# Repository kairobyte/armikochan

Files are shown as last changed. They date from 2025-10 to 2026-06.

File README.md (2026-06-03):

# ARMIKOCHAN V2: 8 AXIS ROBOTIC ARM




This project is my 200+ day journey of building a high-precision, 8-degree-of-freedom robotic arm from scratch.

## The Vision

Most robotic arms out there are 6DOF at best, and they easily cost upwards of $5000. For a student or a smaller college, that's just not realistic. The ones that do offer more capability are either proprietary, locked behind expensive licenses, or simply too complex to learn from. There's a huge gap between what's available and what's actually accessible, and that gap is what this project is trying to fill.

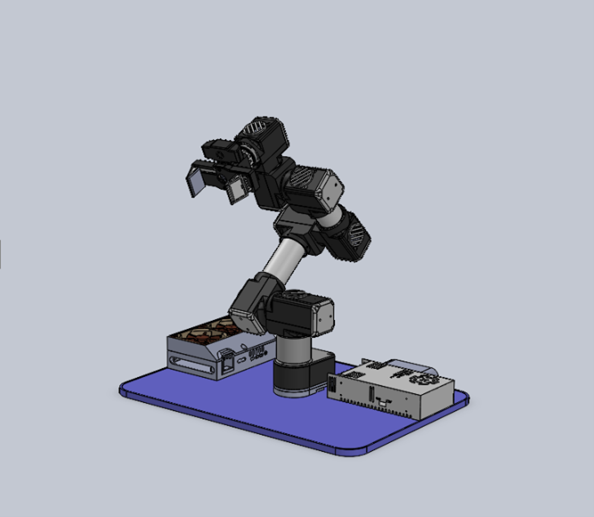
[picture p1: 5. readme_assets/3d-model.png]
3d-model
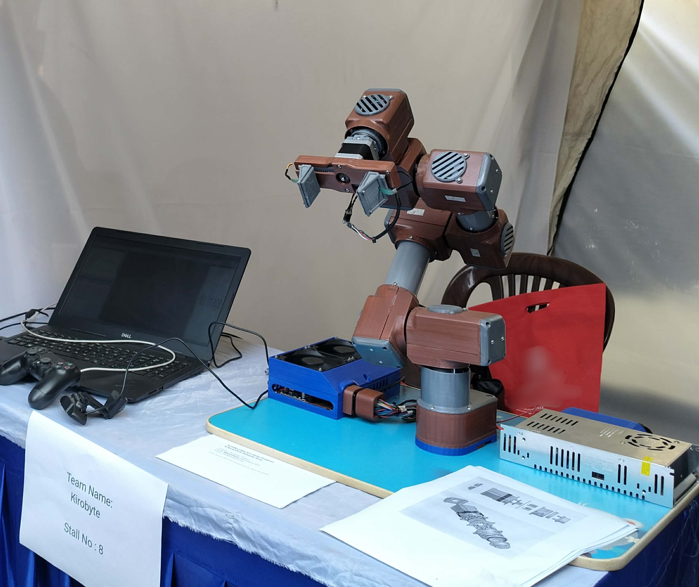
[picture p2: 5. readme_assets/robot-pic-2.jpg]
robot image
 

## Repository Contents

- **`/1. firmware`**: ESP32 code for low-latency motor driving and FSR sensor processing.
- **`/2. ros_ws`**: The heart of the robot. Contains the URDF, MoveIt2 configurations, and MoveIt Servo nodes for real-time control.
- **`/3. 3D Model`**: 3D models (STL/SLDPRT) including my custom-designed planetary gear systems.
- **`/4. docs`**: Technical blogs and design notes.
- **`/5. readme_assets`**: Contains images for README.md file

## Tech Stack

- **Software:** Ubuntu 24.04, ROS2 Jazzy, MoveIt2, Solidworks, OpenCV
- **Brain:** PC/Laptop <-> Raspberry Pi <-> ESP32.
- **Actuators:** Nema 17 Stepper Motor, with custom designed planetary gear set.
- **Feedback:** Force-Sensitive Resistors (FSR) with silicone layer for gripper feedback and AS5600 magnetic encoder for joint angle feedback.

## Block Diagram
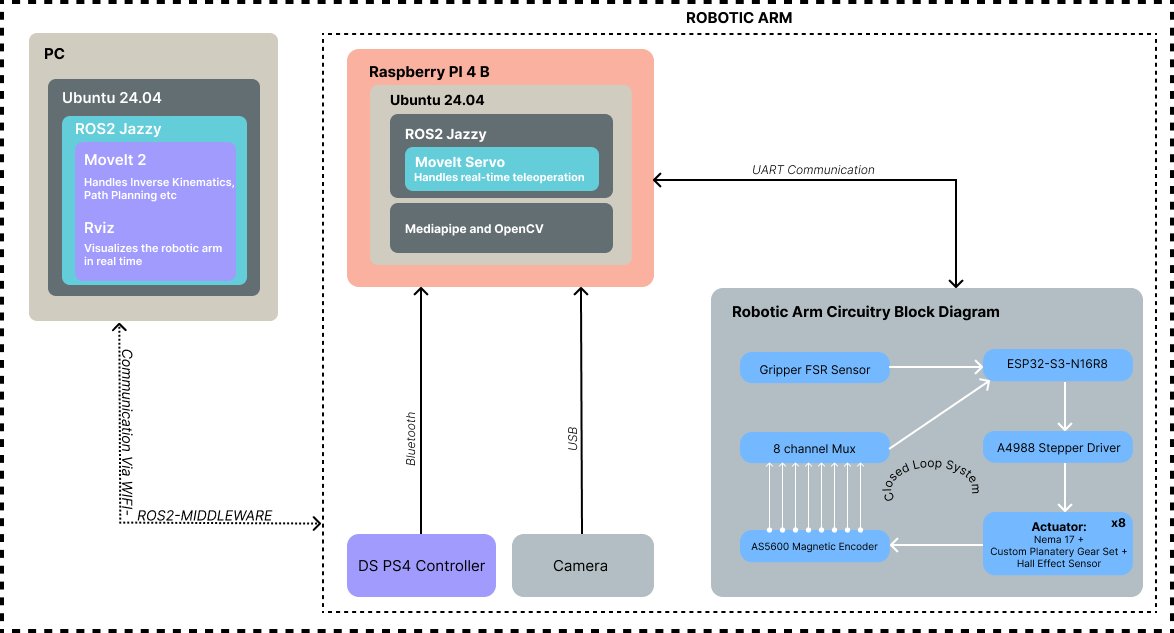
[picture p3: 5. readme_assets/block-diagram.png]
block diagram


## Community & Support

I am a solo student developer balancing college, coding, and hardware. If you find this project helpful:

- **Follow the Journey:** [@kairobyte](https://instagram.com/kairobyte) on Instagram.
- **Visit the Site:** [kairobyte.com](https://kairobyte.com) for in-depth engineering blogs.

## Getting Started

```bash
# Clone the repository
git clone https://github.com/kairobyte/armikochan.git

# Navigate to the workspace
cd armikochan/2.\ ros_ws/

# Build the project
colcon build --symlink-install

# Source and Launch (Refer to /docs for specific launch files)
source install/setup.bash
```

## Next Steps:

- The shoulder joint could be made bidirectional, which would help reduce the sag a lot.
- Using slip rings instead of passing the wires through the cavity inside the actuators would significantly increase the workspace of the arm.

Lastly, I'll be the first to admit, building something like this alone is difficult. And when you're doing it all by yourself, your perspective is limited. So not everything is done the most efficient way, and there's honestly a lot of room for improvement.

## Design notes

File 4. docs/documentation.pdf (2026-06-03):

### 8 AXIS ROBOTIC ARM

An open source, 8-axis ROS2 robotic arm built from scratch to automate complex tasks. Sushant Thakur (2nd year EE)

The Problem:
Most robotic arms out there are 6DOF at best, and they easily cost upwards of $5000. For a student or a smaller college, that's just not realistic. The ones that do oer more capability are either proprietary, locked behind expensive licenses, or simply too complex to learn from. There's a huge gap between what's available and what's actually accessible, and that gap is what this project is trying to fill.

Idea:

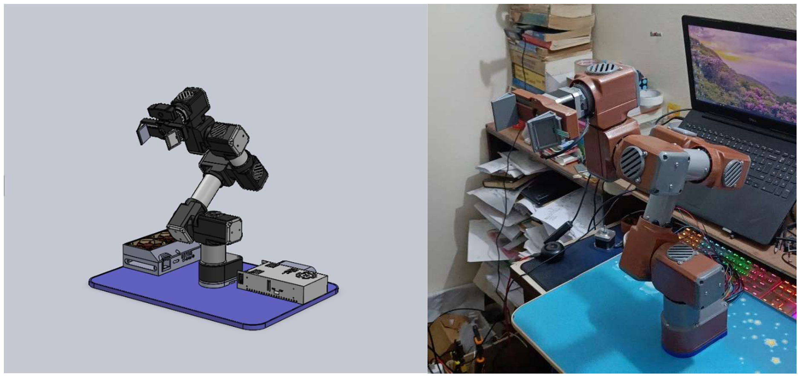
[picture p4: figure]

Figure 1: Real-Life Model | Figure 2: 3D-Model
In daily life and across industries, there are countless repetitive tasks that people want to automate, material handling, packaging, assembly, welding etc. Robotic arms are at the core of all of that, whether it's healthcare, research labs, nuclear facilities, or even space. But the problem is, most robotic arms are expensive and out of reach for students and smaller institutions. So, I built an 8DOF industrial robotic arm from scratch for under $500 and made it completely open source at https://github.com/kairobyte/armikochan, so anyone with a 3D printer and basic electronics can build one, learn from it, and make it better.

How It Works:

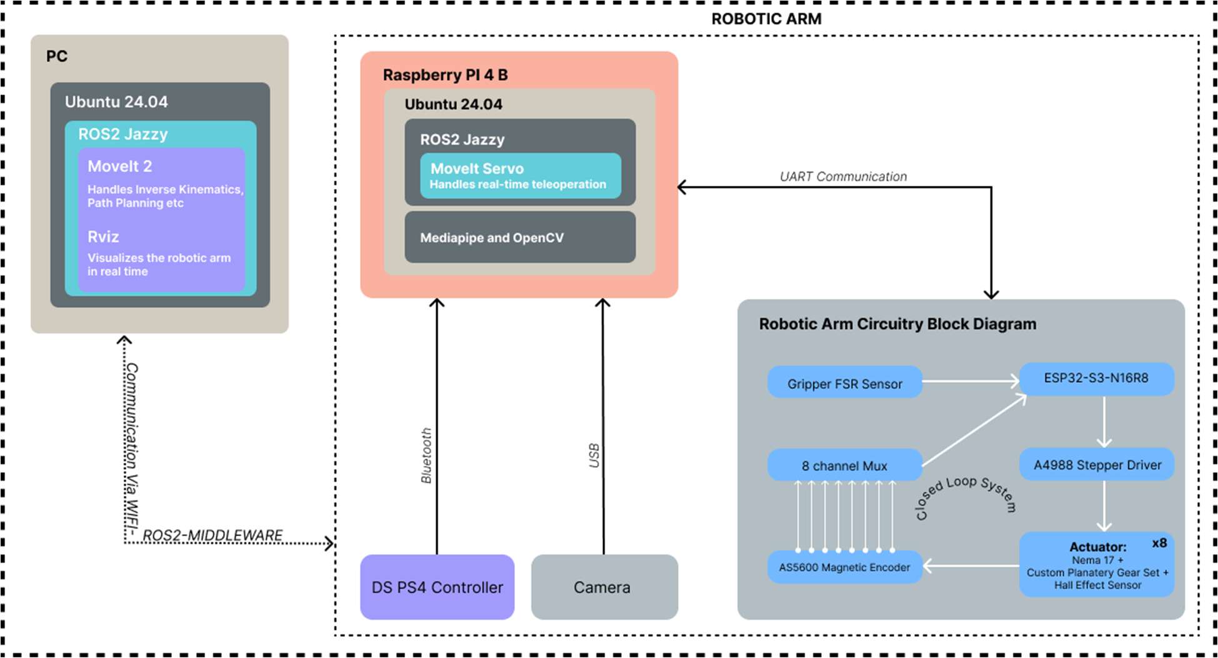
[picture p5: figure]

Figure 3: System Layout Diagram
There are two main parts that work together to get things done. Both the PC and the Raspberry Pi run ROS2 Jazzy, which keeps the communication between them really reliable. The PC handles the heavier stu like Inverse Kinematics, Path Planning, and real-time visualization. The Raspberry Pi takes care of the simpler but time-sensitive tasks like processing camera data.
The robotic arm itself has six main components. The microcontroller is an ESP32-S3-N16R8, and it has enough pins to handle everything I needed to connect, 9 stepper motors, 9 hall eect sensors, and FSR sensors. That's a lot of connections, and most other microcontrollers just don't cut it. For movement, I used Nema 17 stepper motors. The torque isn't enough on their own, so I designed a dual stage planetary gear system that trades some RPM for a much higher torque output.
When a move command comes in through the joystick, the Raspberry Pi picks it up first. MoveIt Servo then breaks that movement into smaller incremental commands, keeping the delay under 40ms from command to execution.
The whole system runs as a closed loop, meaning the arm can correct itself if something pushes it o position. A PID controller checks each joint angle at 40Hz, and if anything is o, it smoothly adjusts back to where it should be.

Result:
In simulation, the arm had an accuracy of about ±4mm. In real life though, things like plastic flex and backlash in the actuators brought that down to around ±2cm, which is expected, and it’s something that can be improved with better materials down the line. The gripper can apply anywhere between 0.4N to 1.5N of force, and the user can adjust that depending on how hard or soft the object is. Adding a thin layer of silicone over the gripper made a noticeable dierence too. It increased the friction on the grabbing surface and made the whole thing a lot more reliable. And finally, having those 2 extra degrees of freedom really paid o, the arm was able to avoid obstacles while still doing its task, which is something most budget arms simply can't do.

Challenges:
Designing the planetary gear system in such a tight space, with an outer diameter of just 43mm, was one of the harder parts of this build. The planet gears have really fine teeth, and 3D printing just isn't precise enough at that scale. It works, but it's definitely a weak point. Another issue was the wiring. The stepper wires and the feedback wires from the AS5600 encoder were running right next to each other, and the electromagnetic interference from the stepper wires was corrupting the feedback signal, making the data unreliable. I fixed this by bumping up the voltage on the feedback line, slowing down the I2C clock speed, binding the wires together, and writing a software debouncing algorithm. Using shielded STP wires would've probably been a cleaner fix, and that's something worth trying in the next version. Lastly, the motors actually produce more torque than the plastic parts can handle. So, at the end of the day, the plastic is the bottleneck, not the motors.

Next Steps:
There's definitely room to improve the design. For example, the shoulder joint could be made bidirectional, which would help reduce the sag a lot. Switching from plastic to metal parts would also make a big dierence, both in accuracy and how reliable the whole system is. The wiring situation could be cleaner too. Right now, the wires pass through a cavity inside the actuator, which limits how far each joint can rotate. Using slip rings instead would remove that limitation and significantly increase the workspace area of the arm.

Team and Tools:
This entire project was done by me, from designing the joints to programming the microcontroller to putting together the electronics. I used SolidWorks for all the 3D design work, and ROS2 for building the control system. For the PCB, I designed everything in KiCad, but in the end I just went with a matrix board and soldered the components by hand. Now, I'll be the first to admit, building something like this alone is diicult. And when you're doing it all by yourself, your perspective is limited. So not everything is done the most eicient way, and there's honestly a lot of room for improvement.

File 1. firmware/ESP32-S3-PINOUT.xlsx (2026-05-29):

 |  |  | ESP32-S3-N16R8 Pin Out
 |  | 3V | 1 |  |  | 44 | GND
 |  | 3V | 2 |  |  | 43 | GPIO 43 | U0TXD | CLK_OUT
 |  | RST | 3 |  |  | 42 | GPIO 44 | U0RXD | CLK_OUT
TOUCH | ADC1_CH3 | GPIO 4 | 4 | DIR_1 | G_FSR | 41 | GPIO 1 | ADC | TOUCH
TOUCH | ADC1_CH4 | GPIO 5 | 5 | DIR_2 | G_HALL | 40 | GPIO 2 | ADC | TOUCH
TOUCH | ADC1_CH5 | GPIO 6 | 6 | DIR_3 | HALL_8 | 39 | GPIO 42 | MTMS |  |  |  | Custom Connector Pin Out
TOUCH | ADC1_CH6 | GPIO 7 | 7 | DIR_4 | HALL_7 | 38 | GPIO 41 | MTDI | CLK_OUT
SDA | ADC2_CH4 | GPIO 15 | 8 |  | HALL_6 | 37 | GPIO 40 | MTDO | CLK_OUT
SCL | ADC2_CH5 | GPIO 16 | 9 |  | HALL_5 | 36 | GPIO 39 | MTCK | CLK_OUT | 1A | 1B | VCC | SCL | HALL | SDA | GND | 2B | 2A
U1TXD | ADC2_CH6 | GPIO 17 | 10 | DIR_5 | G_DIR | 35 | GPIO 38
U1TRXD | ADC2_CH7 | GPIO 18 | 11 | DIR_6 | G_STEP | 34 | GPIO 37
TOUCH | ADC1_CH7 | GPIO 8 | 12 | DIR_7 | HALL_4 | 33 | GPIO 36 |  |  |  |  |  | 2B | 2A | 1B | 1A
TOUCH | ADC1_CH2 | GPIO 3 | 13 | DIR_8 | HALL_3 | 32 | GPIO 35 |  |  |  |  | GND | SDA | HALL | SCL | VCC
 |  | GPIO 46 | 14 |  |  | 31 | GPIO 0
TOUCH | ADC | GPIO 9 | 15 | STEP_1 | HALL_2 | 30 | GPIO 45
TOUCH | ADC | GPIO 10 | 16 | STEP_2 | HALL_1 | 29 | GPIO 48
TOUCH | ADC | GPIO 11 | 17 | STEP_3 | STEP_8 | 28 | GPIO 47
TOUCH | ADC | GPIO 12 | 18 | STEP_4 | STEP_7 | 27 | GPIO 21
TOUCH | ADC | GPIO 13 | 19 | STEP_5 |  | 26 | GPIO 20 | ADC | CLK_OUT
TOUCH | ADC | GPIO 14 | 20 | STEP_6 |  | 25 | GPIO 19 | ADC | CLK_OUT
 |  | 5V | 21 |  |  | 24 | GND
 |  | GND | 22 |  |  | 23 | GND
 |  |  | Shouldn't be used

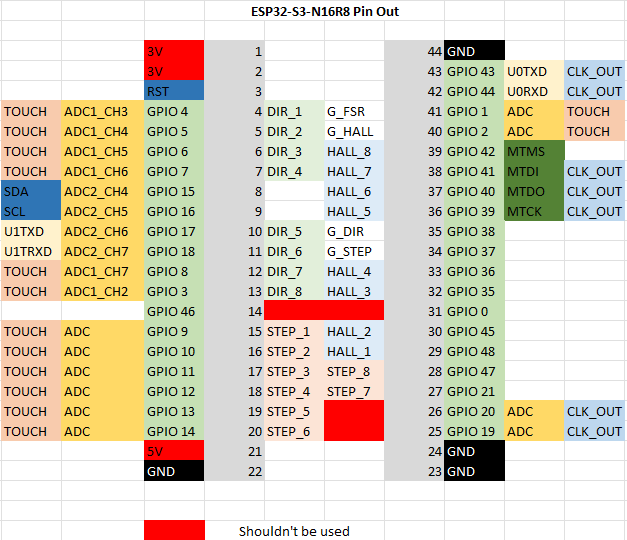
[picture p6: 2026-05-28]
1. firmware/pin_out.png

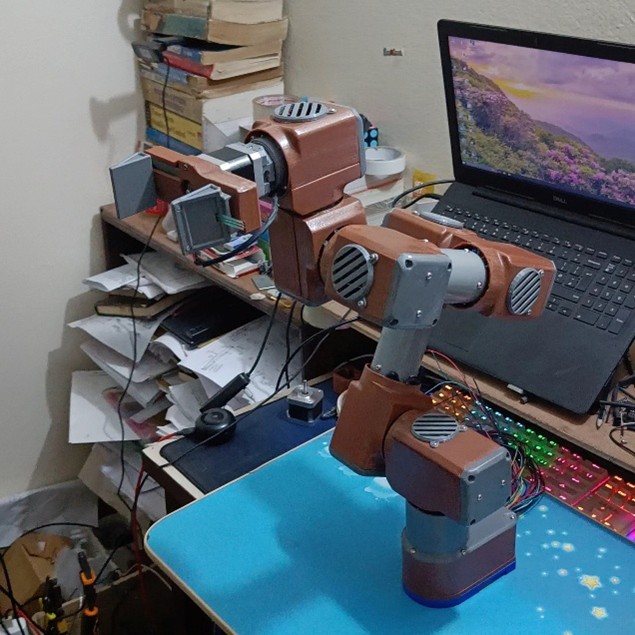
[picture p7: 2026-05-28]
5. readme_assets/robot-pic-1.jpg

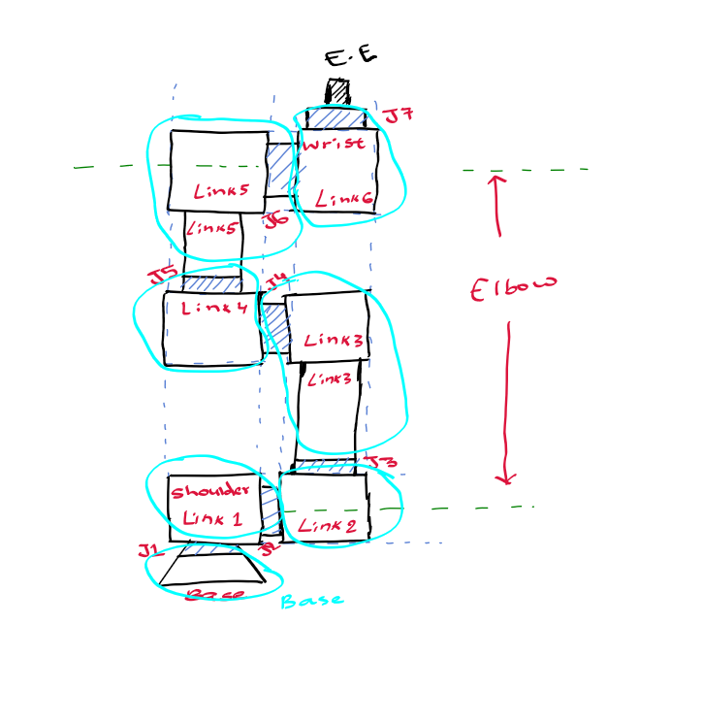
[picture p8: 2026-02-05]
3. 3D Model/layout.png

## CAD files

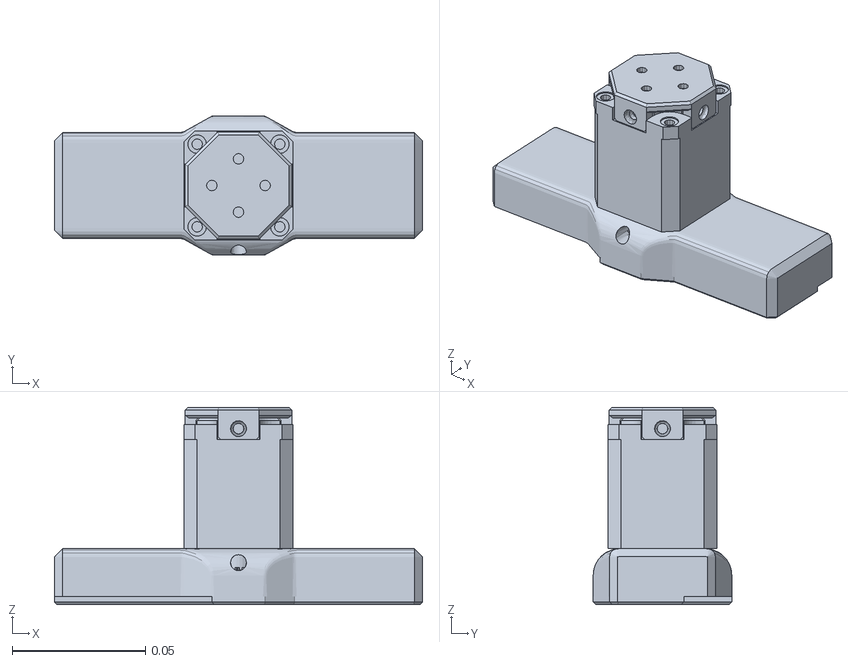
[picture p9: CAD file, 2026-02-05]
2. ros_ws/src/arm_description/meshes/tool_link.STL
0.138 x 0.052 x 0.074

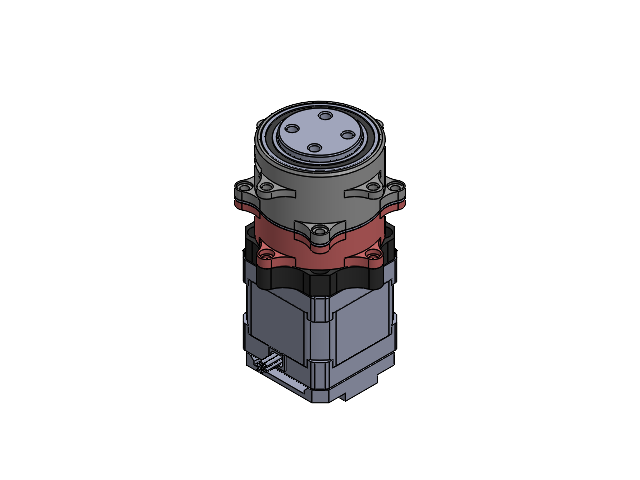
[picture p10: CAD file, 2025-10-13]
3. 3D Model/0. Components/1. Planetary_Gear/planetary_gear_asm.SLDASM
nema17_40mm.step
AS5600-stepper-connector-test
stepper-holder-upper
sun-gear
ring-gear
planet-gear-holder-top-layer
ring-gear-layer-2
top-layer-cover
68062rs.stp

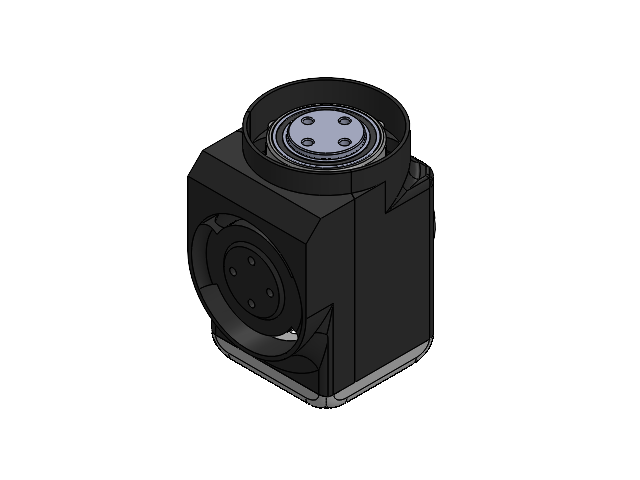
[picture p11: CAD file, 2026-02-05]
3. 3D Model/3. Elbow/1. Link_2/joint/link_2.SLDASM
link_2-planet-gear-holder-top-layer
link_2-ring-gear-layer-2
68062rs.stp
link_2-
link_2-right-angle-joint-circular-cover
link_2-right-angle-joint-type2

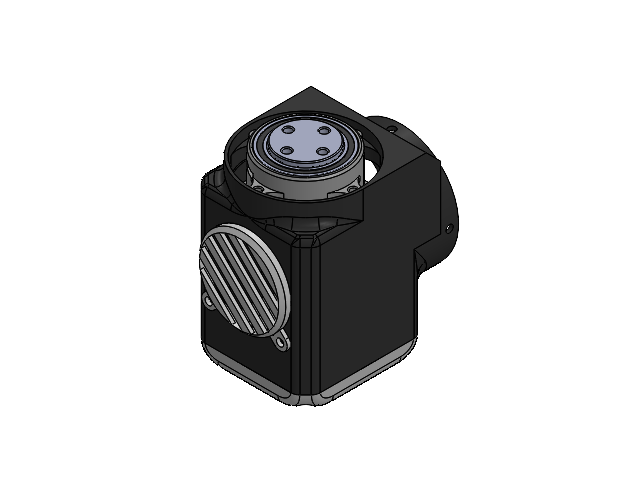
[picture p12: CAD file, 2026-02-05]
3. 3D Model/3. Elbow/2. Link_3/joint/link_3-joint.SLDASM
link_3-right-angle-joint-type3
link_3-ring-gear-layer-2
link_3-planet-gear-holder-top-layer
link_3-right-angle-joint-circular-cover
link_3-right-angle-joint-cover
68062rs.stp

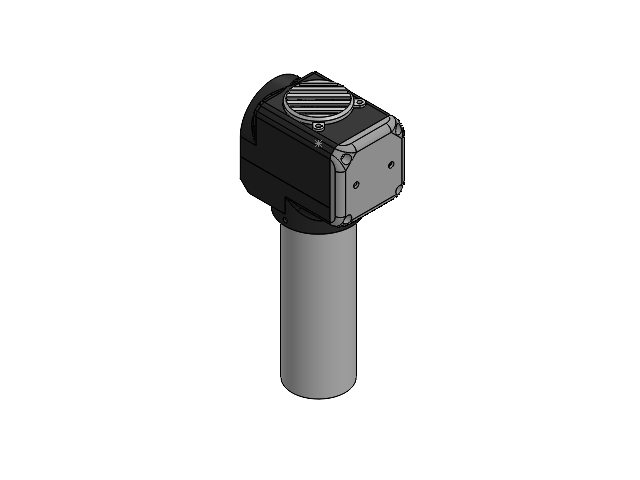
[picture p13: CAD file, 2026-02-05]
3. 3D Model/3. Elbow/2. Link_3/link-3-main.SLDASM
elbow_link3
l1_elbow_linker
l1_connector_angle
link_3-right-angle-joint-type3
link_3-ring-gear-layer-2
link_3-planet-gear-holder-top-layer
link_3-right-angle-joint-circular-cover
link_3-right-angle-joint-cover
68062rs.stp

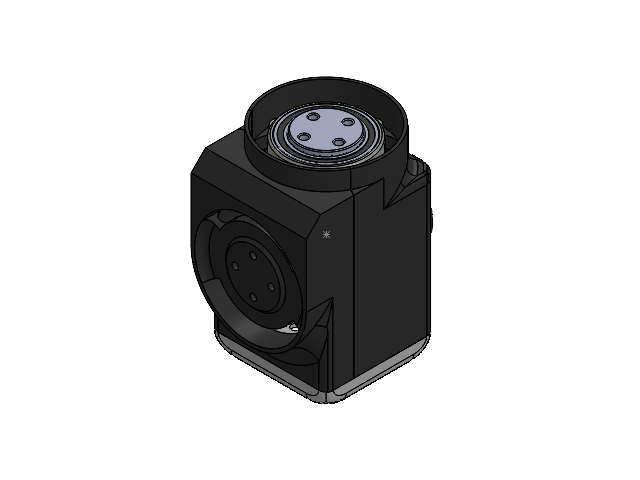
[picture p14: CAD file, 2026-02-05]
3. 3D Model/3. Elbow/3. Link_4/link_4-main.SLDASM
link_4-right-angle-joint-cover
link_4-right-angle-joint-type2
link_4-ring-gear-layer-2
link_4-planet-gear-holder-top-layer
link_4-right-angle-joint-circular-cover
68062rs.stp

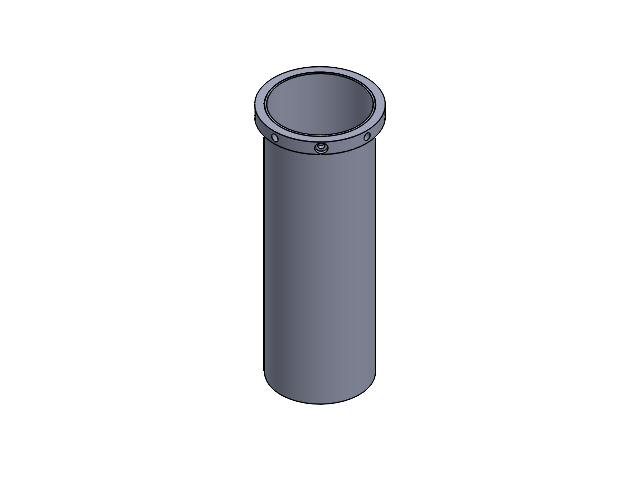
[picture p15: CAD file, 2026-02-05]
3. 3D Model/3. Elbow/4. Link_5/link/link_5_link_asm.SLDASM
link-5_elbow
l1_elbow_linker
l1_connector_angle

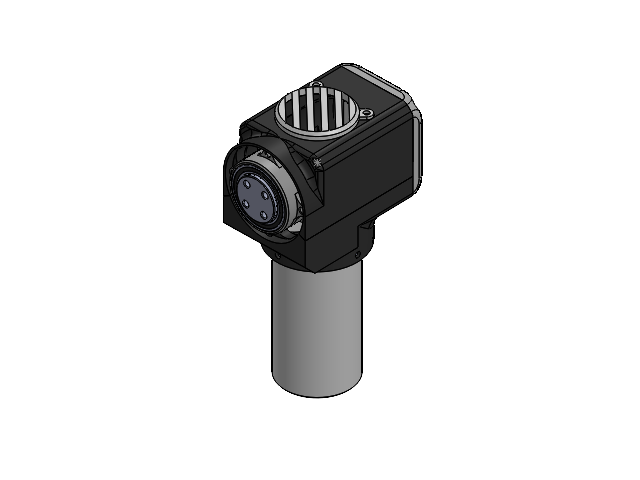
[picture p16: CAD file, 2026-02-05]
3. 3D Model/3. Elbow/4. Link_5/link_5-main.SLDASM
link-5_elbow
l1_elbow_linker
l1_connector_angle
link_5-planet-gear-holder-top-layer
link_5-right-angle-joint-circular-cover
link_5-right-angle-joint-cover
link_5-right-angle-joint-type3
link_5-ring-gear-layer-2
68062rs.stp

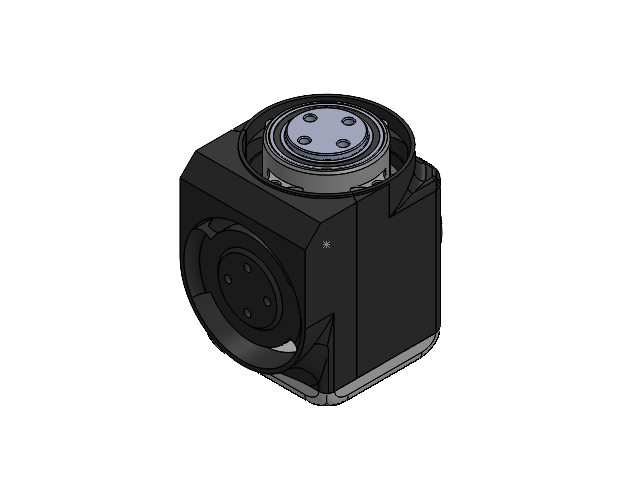
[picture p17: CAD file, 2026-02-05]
3. 3D Model/4. Wrist/wrist-main.SLDASM
68062rs.stp
wrist-planet-gear-holder-top-layer
wrist-right-angle-joint-circular-cover
wrist-right-angle-joint-cover
wrist-right-angle-joint-type1
wrist-ring-gear-layer-2
wrist-stepper-holder-upper

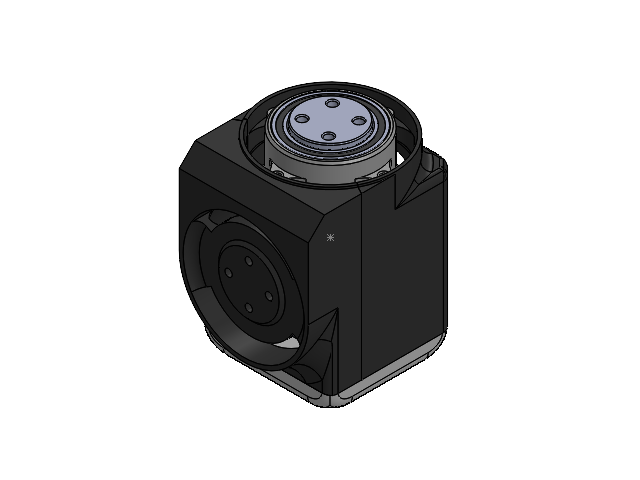
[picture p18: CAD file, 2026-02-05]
3. 3D Model/4.1 ee_wrist/ee_wrist_main.SLDASM
ee_wrist-nema17_40mm.step
ee_wrist-right-angle-joint-cover
ee_wrist-right-angle-joint-type1
ee_wrist-ring-gear-layer-2
ee_wrist-stepper-holder-upper
ee_wrist-68062rs.stp
ee_wrist-AS5600-stepper-connector-test
ee_wrist-planet-gear-holder-top-layer

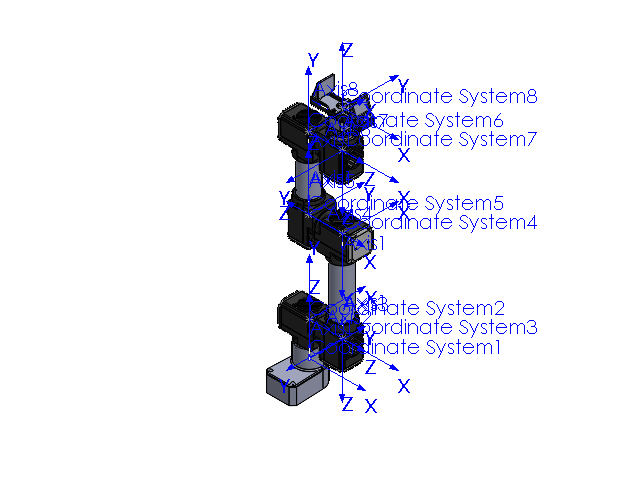
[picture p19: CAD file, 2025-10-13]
3. 3D Model/main-3d-model.SLDASM
planet-gear-holder-top-layer
ring-gear
ring-gear-layer-2
stepper-holder-upper
top-layer-cover
68062rs.stp x 7
base-holder
base-holder-top
nema17_40mm.step x 6
shoulder_AS5600-stepper-connector-test
shoulder_right-angle-joint-cover
shoulder_planet-gear-holder-top-layer
shoulder_right-angle-joint-type1
shoulder_right-angle-upper-cover
shoulder_ring-gear
shoulder_ring-gear-layer-2
shoulder_stepper-holder-upper
shoulder_top-layer-cover
link_2-stepper-holder-upper
link_2-AS5600-stepper-connector-test
link_2-planet-gear-holder-top-layer
link_2-ring-gear
link_2-ring-gear-layer-2
link_2-top-layer-cover
link_2-
link_2-right-angle-joint-circular-cover
link_2-right-angle-joint-type2
elbow_link3
l1_elbow_linker x 2
l1_connector_angle x 2
link_3-right-angle-joint-type3
link_3-ring-gear
link_3-ring-gear-layer-2
link_3-stepper-holder-upper
link_3-top-layer-cover
link_3-AS5600-stepper-connector-test
link_3-planet-gear-holder-top-layer
link_3-right-angle-joint-circular-cover
link_3-right-angle-joint-cover
link_4-right-angle-joint-cover
link_4-right-angle-joint-type2
link_4-ring-gear
link_4-ring-gear-layer-2
link_4-stepper-holder-upper
link_4-top-layer-cover
link_4-AS5600-stepper-connector-test
link_4-planet-gear-holder-top-layer
link_4-right-angle-joint-circular-cover
link-5_elbow
link_5-AS5600-stepper-connector-test
link_5-planet-gear-holder-top-layer
link_5-right-angle-joint-circular-cover
link_5-right-angle-joint-cover
link_5-right-angle-joint-type3
link_5-ring-gear
link_5-ring-gear-layer-2
link_5-stepper-holder-upper
link_5-top-layer-cover
wrist-top-layer-cover
wrist-AS5600-stepper-connector-test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

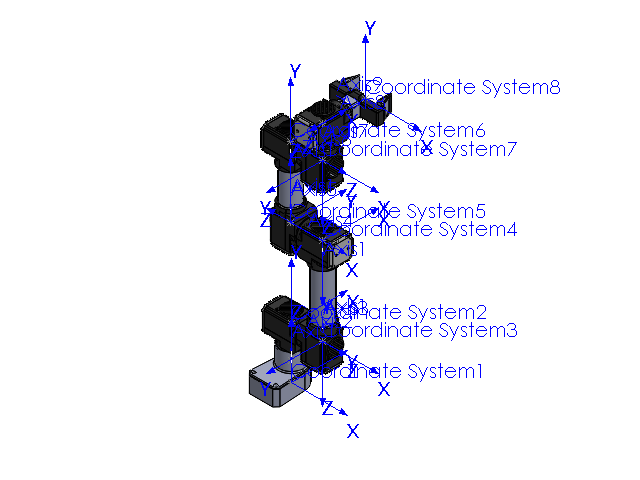
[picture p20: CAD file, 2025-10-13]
3.1. arm_model_main/main-3d-model-simple.SLDASM
planet-gear-holder-top-layer
ring-gear
ring-gear-layer-2
stepper-holder-upper
top-layer-cover
68062rs.stp x 7
base-holder
base-holder-top
shoulder_right-angle-joint-cover
shoulder_planet-gear-holder-top-layer
shoulder_right-angle-joint-type1
shoulder_right-angle-upper-cover
shoulder_ring-gear-layer-2
link_2-planet-gear-holder-top-layer
link_2-ring-gear-layer-2
link_2-
link_2-right-angle-joint-circular-cover
link_2-right-angle-joint-type2
elbow_link3
l1_elbow_linker x 2
l1_connector_angle x 2
link_3-right-angle-joint-type3
link_3-ring-gear-layer-2
link_3-planet-gear-holder-top-layer
link_3-right-angle-joint-circular-cover
link_3-right-angle-joint-cover
link_4-right-angle-joint-cover
link_4-right-angle-joint-type2
link_4-ring-gear-layer-2
link_4-AS5600-stepper-connector-test
link_4-planet-gear-holder-top-layer
link_4-right-angle-joint-circular-cover
link-5_elbow
link_5-AS5600-stepper-connector-test
link_5-planet-gear-holder-top-layer
link_5-right-angle-joint-circular-cover
link_5-right-angle-joint-cover
link_5-right-angle-joint-type3
link_5-ring-gear-layer-2
wrist-AS5600-stepper-connector-test
wrist-planet-gear-holder-top-layer
wrist-right-angle-joint-circular-cover
wrist-right-angle-joint-cover
wrist-right-angle-joint-type1
wrist-ring-gear-layer-2
ee_wrist-nema17_40mm.step
ee_wrist-right-angle-joint-cover
ee_wrist-right-angle-joint-type1
ee_wrist-ring-gear-layer-2
ee_wrist-stepper-holder-upper
ee_wrist-68062rs.stp
ee_wrist-AS5600-stepper-connector-test
ee_wrist-planet-gear-holder-top-layer
ee_wrist-right-angle-joint-circular-cover
ef_stepper-holder-gripper
ef_pinion-gear
ef_support-gear x 2
ef_gripper-cover
ef_upper-grip x 2
ee_stepper-connector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

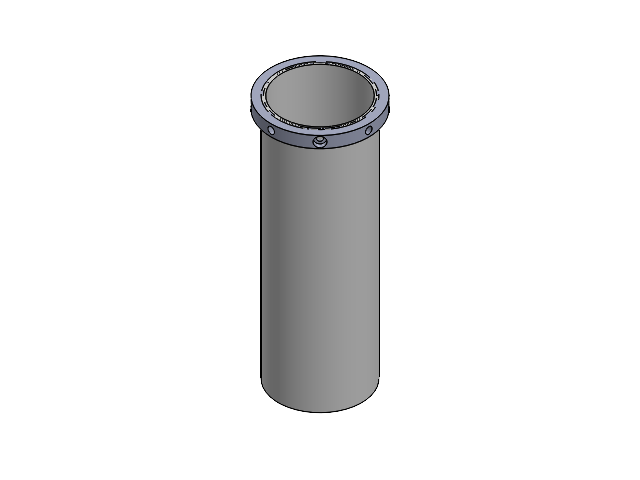
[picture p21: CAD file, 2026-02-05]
3. 3D Model/3. Elbow/2. Link_3/link/link_3.SLDASM
elbow_link3
l1_elbow_linker
l1_connector_angle

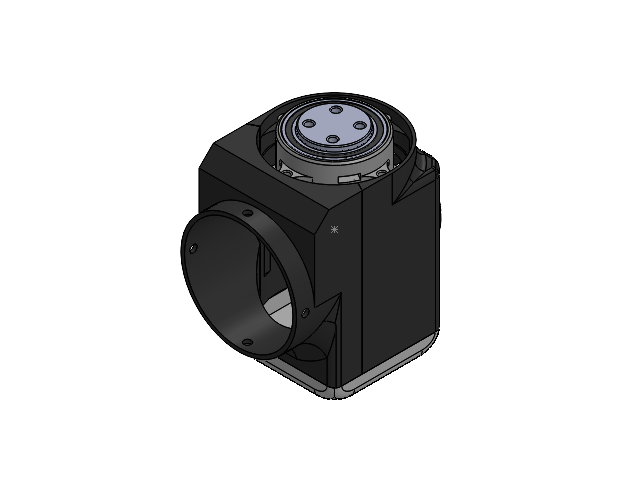
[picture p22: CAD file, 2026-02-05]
3. 3D Model/3. Elbow/4. Link_5/joint/link_5-joint-asm.SLDASM
link_5-planet-gear-holder-top-layer
link_5-right-angle-joint-circular-cover
link_5-right-angle-joint-cover
link_5-right-angle-joint-type3
link_5-ring-gear-layer-2
68062rs.stp

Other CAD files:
3. 3D Model/2. Shoulder/joint/shoulder_assembly.SLDASM
3. 3D Model/1. Base/base_asm.SLDASM
3. 3D Model/5. End_Effector/ef_main-assembly.SLDASM
3. 3D Model/5. End_Effector/ee_fsr_assembly.SLDASM
2. ros_ws/src/arm_description/meshes/base_link.STL
2. ros_ws/src/arm_description/meshes/cam_link.STL
2. ros_ws/src/arm_description/meshes/grip_left_link.STL
2. ros_ws/src/arm_description/meshes/grip_right_link.STL
2. ros_ws/src/arm_description/meshes/link_1.STL
2. ros_ws/src/arm_description/meshes/link_2.STL
2. ros_ws/src/arm_description/meshes/link_3.STL
2. ros_ws/src/arm_description/meshes/link_4.STL
2. ros_ws/src/arm_description/meshes/link_5.STL
2. ros_ws/src/arm_description/meshes/link_6.STL
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

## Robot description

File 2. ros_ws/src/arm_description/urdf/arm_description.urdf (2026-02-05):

<?xml version="1.0" encoding="utf-8"?>
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
<robot name="arm_description">
  <link name="world" />
  <joint name="world_to_base" type="fixed">
    <parent link="world" />
    <child link="base_link" />
    <origin xyz="0 0 0" rpy="0 0 0" />
  </joint>
  <link name="base_link">
    <inertial>
      <origin xyz="0.013005483231454 -0.0122874534188383 -0.0125058754014893" rpy="0 0 0" />
      <mass value="3.38588071798989" />
      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
    </inertial>
    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
  </link>
  <link name="link_1">
    <inertial>
      <origin xyz="-0.00573535850787753 -1.51814079566992E-05 0.141615303230785" rpy="0 0 0" />
      <mass value="0.163183381078305" />
      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
    </inertial>
    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
  </link>
  <joint name="joint_1" type="revolute">
    <origin xyz="0 0 0" rpy="0 0 0" />
    <parent link="base_link" />
    <child link="link_1" />
    <axis xyz="0 0 1" />
    <limit lower="-0.7854" upper="0.8727" effort="200" velocity="5" />
  </joint>
  <link name="link_2">
    <inertial>
      <origin xyz="-5.33969957444702E-07 0.00596557002640269 0.0841628003852398" rpy="0 0 0" />
      <mass value="0.141380673625224" />
      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
    </inertial>
    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
  </link>
  <joint name="joint_2" type="revolute">
    <origin xyz="0 0 0.1464" rpy="1.5707963267949 0 1.5707963267949" />
    <parent link="link_1" />
    <child link="link_2" />
    <axis xyz="0 0 1" />
    <limit lower="-1.57" upper="1.57" effort="200" velocity="10" />
  </joint>
  <link name="link_3">
    <inertial>
      <origin xyz="-0.00391173104561557 -1.49146629101343E-05 -0.170024735109497" rpy="0 0 0" />
      <mass value="0.177195737003072" />
      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
    </inertial>
    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
  </link>
  <joint name="joint_3" type="revolute">
    <origin xyz="0 0 0.0895" rpy="1.5707963267949 -1.5707963267949 0" />
    <parent link="link_2" />
    <child link="link_3" />
    <axis xyz="0 0 -1" />
    <limit lower="-0.7854" upper="0.7854" effort="200" velocity="10" />
  </joint>
  <link name="link_4">
    <inertial>
      <origin xyz="-3.6973238745408E-05 -0.00339659287195743 0.0858843482112302" rpy="0 0 0" />
      <mass value="0.148325167434625" />
      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
    </inertial>
    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
  </link>
  <joint name="joint_4" type="revolute">
    <origin xyz="0 0 -0.197985205862429" rpy="1.5707963267949 0 -1.5707963267949" />
    <parent link="link_3" />
    <child link="link_4" />
    <axis xyz="0 0 1" />
    <limit lower="-2.0944" upper="2.35629" effort="200" velocity="10" />
  </joint>
  <link name="link_5">
    <inertial>
      <origin xyz="0.00209491150541927 -2.80223931179713E-05 0.131173689025555" rpy="0 0 0" />
      <mass value="0.168747212516084" />
      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
    </inertial>
    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
  </link>
  <joint name="joint_5" type="revolute">
    <origin xyz="0 0 0.0909852058624292" rpy="1.5707963267949 1.5707963267949 0" />
    <parent link="link_4" />
    <child link="link_5" />
    <axis xyz="0 0 1" />
    <limit lower="-1.57" upper="1.57" effort="200" velocity="10" />
  </joint>
  <link name="link_6">
    <inertial>
      <origin xyz="3.15012006844584E-05 0.00831132272524687 0.0856917113309387" rpy="0 0 0" />
      <mass value="0.141722203528696" />
      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
    </inertial>
    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
  </link>
  <joint name="joint_6" type="revolute">
    <origin xyz="0 0 0.14698520586243" rpy="1.5707963267949 0 1.5707963267949" />
    <parent link="link_5" />
    <child link="link_6" />
    <axis xyz="0 0 1" />
    <limit lower="-1.57" upper="2.0944" effort="200" velocity="10" />
  </joint>
  <link name="link_7">
    <inertial>
      <origin xyz="3.18264428398052E-05 -0.00373171577154271 -0.0872550227993109" rpy="0 0 0" />
      <mass value="0.201974313822122" />
      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
    </inertial>
    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
  </link>
  <joint name="joint_7" type="revolute">
    <origin xyz="0 0 0.0909852058624295" rpy="1.5707963267949 -1.5707963267949 0" />
    <parent link="link_6" />
    <child link="link_7" />
    <axis xyz="0 0 -1" />
    <limit lower="-2.3529" upper="2.3529" effort="200" velocity="10" />
  </joint>
  <link name="tool_link">
    <inertial>
      <origin xyz="-3.2679917184586E-06 5.5190473645772E-05 0.0296763969651909" rpy="0 0 0" />
      <mass value="0.153175305780123" />
      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
    </inertial>
    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
  </link>
  <joint name="tool_joint" type="revolute">
    <origin xyz="0 -0.124485205862441 -0.0909852058624322" rpy="-1.5707963267949 0 0" />
    <parent link="link_7" />
    <child link="tool_link" />
    <axis xyz="0 0 -1" />
    <limit lower="-3.49" upper="3.49" effort="200" velocity="5" />
  </joint>
  <link name="grip_left_link">
    <inertial>
      <origin xyz="-0.0472057386689508 -0.00225339802100577 0.0018966503911423" rpy="0 0 0" />
      <mass value="0.0199960953484895" />
      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
    </inertial>
    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
  </link>
  <joint name="grip_left_joint" type="prismatic">
    <origin xyz="0 0 -0.0135" rpy="0 0 0" />
    <parent link="tool_link" />
    <child link="grip_left_link" />
    <axis xyz="-1 0 0" />
    <limit lower="-0.04" upper="0" effort="1" velocity="5" />
  </joint>
  <link name="grip_right_link">
    <inertial>
      <origin xyz="0.0472057386690341 0.00225339802100577 0.00189665039114228" rpy="0 0 0" />
      <mass value="0.0199960953484896" />
      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
    </inertial>
    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
  </link>
  <joint name="grip_right_joint" type="prismatic">
    <origin xyz="0 0 -0.0135" rpy="0 0 0" />
    <parent link="tool_link" />
    <child link="grip_right_link" />
    <axis xyz="-1 0 0" />
    <limit lower="0" upper="0.04" effort="1" velocity="5" />
  </joint>
  <link name="cam_link">
    <inertial>
      <origin xyz="0.00500000001588322 0.0402001871503386 0.045389460364602" rpy="0 0 0" />
      <mass value="0.065967932601823" />
      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
    </inertial>
    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
  </link>
  <joint name="cam_joint" type="fixed">
    <origin xyz="0 0 -0.0135" rpy="0 0 0" />
    <parent link="tool_link" />
    <child link="cam_link" />
    <axis xyz="0 0 0" />
  </joint>
</robot>

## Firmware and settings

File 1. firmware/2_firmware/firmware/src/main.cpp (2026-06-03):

/*******************************************************************************
 * FILENAME:    main.cpp
 * DESCRIPTION: The actual code running on esp32 in the final project
 * AUTHOR:      Sushant Thakur
 * DATE:        202-05-29
 * VERSION:     1.0.0
 * 
 * COPYRIGHT:   Copyright (c) 2026 Sushant Thakur. All rights reserved.
 ******************************************************************************/

// ============================================================================
// File: main.cpp
// Auto-added section markers and high-level comments
// ============================================================================

// ====== Includes ======
#include <Arduino.h>
#include <AccelStepper.h>

// ────────────────────────────────────────────────
// Configuration
// ────────────────────────────────────────────────

// ====== Configuration ======
#define STEPPER_COUNT       9
#define SERIAL_BAUD        115200
#define SERIAL_TIMEOUT_MS   50   // how long to wait for full command

// Pin arrays (make sure these match your wiring!)
// ====== Globals ======
const uint8_t DIR_PINS[STEPPER_COUNT]  = {4, 5, 6, 7, 17, 18, 8, 3, 38};
const uint8_t STEP_PINS[STEPPER_COUNT] = {9,10,11,12,13,14,21,47,37};

// Per-motor tuning (steps/s and steps/s²)
const float MAX_SPEEDS[STEPPER_COUNT]      = {1000, 1200, 1000, 800, 1000, 1000, 1000, 1000, 1000};
const float ACCELERATIONS[STEPPER_COUNT]   = {500, 500, 500, 500, 500, 500, 500, 500, 500};

// Default / home position (in steps)
const long DEFAULT_POSE[STEPPER_COUNT] = {0, 3000, 0, 1500, 0, 1000, 0, 0, 0};

// Gripper specifics
const long GRIPPER_OPEN_POS = 0;
const long GRIPPER_MAX_CLOSE_POS = -400; // Large negative value to keep moving until FSR triggers
const int FSR_PIN = 1;
const int FSR_THRESHOLD = 1000;

// ────────────────────────────────────────────────
// Globals
// ────────────────────────────────────────────────

AccelStepper steppers[STEPPER_COUNT] = {
    AccelStepper(AccelStepper::DRIVER, STEP_PINS[0], DIR_PINS[0]),
    AccelStepper(AccelStepper::DRIVER, STEP_PINS[1], DIR_PINS[1]),
    AccelStepper(AccelStepper::DRIVER, STEP_PINS[2], DIR_PINS[2]),
    AccelStepper(AccelStepper::DRIVER, STEP_PINS[3], DIR_PINS[3]),
    AccelStepper(AccelStepper::DRIVER, STEP_PINS[4], DIR_PINS[4]),
    AccelStepper(AccelStepper::DRIVER, STEP_PINS[5], DIR_PINS[5]),
    AccelStepper(AccelStepper::DRIVER, STEP_PINS[6], DIR_PINS[6]),
    AccelStepper(AccelStepper::DRIVER, STEP_PINS[7], DIR_PINS[7]),
    AccelStepper(AccelStepper::DRIVER, STEP_PINS[8], DIR_PINS[8]),
};

long target_positions[STEPPER_COUNT] = {0};

// ────────────────────────────────────────────────
// Compute the expected move time (in seconds) for a given acceleration, max speed, and distance
// ────────────────────────────────────────────────
// Function: compute_move_time
// ====== Functions ======
double compute_move_time(float accel, float max_speed, long distance) {
    distance = abs(distance);
    if (distance == 0) return 0.0;

    float ramp_distance = (max_speed * max_speed) / accel;

    if ((float)distance <= ramp_distance) {
        // Triangular profile (doesn't reach max speed)
        return 2.0 * sqrt((double)distance / accel);
    } else {
        // Trapezoidal profile
        double ramp_time = max_speed / accel;
        double const_distance = distance - ramp_distance;
        double const_time = const_distance / max_speed;
        return 2.0 * ramp_time + const_time;
    }
}

// ────────────────────────────────────────────────
// Fast atoi that handles negative numbers
// ────────────────────────────────────────────────
// Function: fast_atoi
inline long fast_atoi(const char *str) {
    long value = 0;
    bool negative = false;

    if (*str == '-') {
        negative = true;
        str++;
    }

    while (*str >= '0' && *str <= '9') {
        value = value * 10 + (*str - '0');
        str++;
    }

    return negative ? -value : value;
}

// ────────────────────────────────────────────────
// Serial command parser
// ────────────────────────────────────────────────
// Function: read_serial_command
void read_serial_command() {
    if (Serial.available() == 0) return;

    static char buffer[160];
    size_t len = Serial.readBytesUntil('\n', buffer, sizeof(buffer) - 1);

    if (len == 0) return;

    buffer[len] = '\0';

    // Trim leading whitespace
    char *start = buffer;
    while (*start == ' ' || *start == '\t') start++;

    int motor_index = 0;
    char *token = strtok(start, ", ");

    bool valid = true;
    long new_targets[STEPPER_COUNT - 1];
    int gripper_state = 0;

    while (token != nullptr && motor_index < STEPPER_COUNT) {
        if (motor_index < STEPPER_COUNT - 1) {
            new_targets[motor_index] = fast_atoi(token);
        } else {
            gripper_state = fast_atoi(token);
            if (gripper_state != 0 && gripper_state != 1) {
                valid = false;
            }
        }
        motor_index++;
        token = strtok(nullptr, ", ");
    }

    // Check if we got the correct number of values
    if (motor_index != STEPPER_COUNT || token != nullptr) {
        Serial.printf("ERR: expected %d values (8 positions + gripper state 0/1), received %d\n", STEPPER_COUNT, motor_index);
        valid = false;
    }

    if (valid) {
        // Set gripper target based on state
        if (gripper_state == 0) {
            target_positions[8] = GRIPPER_OPEN_POS;
        } else {  // gripper_state == 1
			target_positions[8] = GRIPPER_MAX_CLOSE_POS;
            // int fsr_value = analogRead(FSR_PIN);
            // if (fsr_value > FSR_THRESHOLD) {
            //     target_positions[8] = steppers[8].currentPosition();
            // } else {
            //     target_positions[8] = GRIPPER_MAX_CLOSE_POS;
            // }
        }

        // Compute distances (including gripper for consistency, but exclude from sync)
        long distances[STEPPER_COUNT];
        for (int i = 0; i < STEPPER_COUNT; i++) {
            if (i < STEPPER_COUNT - 1) {
                distances[i] = labs(new_targets[i] - steppers[i].currentPosition());
            } else {
                distances[i] = labs(target_positions[i] - steppers[i].currentPosition());
            }
        }

        // Compute natural move times for the first 8 steppers only
        double natural_times[STEPPER_COUNT];
        double max_time = 0.0;
        for (int i = 0; i < STEPPER_COUNT - 1; i++) {
            natural_times[i] = compute_move_time(ACCELERATIONS[i], MAX_SPEEDS[i], distances[i]);
            if (natural_times[i] > max_time) {
                max_time = natural_times[i];
            }
        }

        // Update the first 8 targets
        memcpy(target_positions, new_targets, sizeof(long) * (STEPPER_COUNT - 1));

        // Scale parameters for each of the first 8 motors to match the max time
        for (int i = 0; i < STEPPER_COUNT - 1; i++) {
            if (distances[i] == 0) {
                steppers[i].moveTo(target_positions[i]);  // Redundant but harmless
                continue;
            }

            double r = max_time / natural_times[i];
            float scaled_speed = MAX_SPEEDS[i] / r;
            float scaled_accel = ACCELERATIONS[i] / (r * r);

            steppers[i].setMaxSpeed(scaled_speed);
            steppers[i].setAcceleration(scaled_accel);
            steppers[i].moveTo(target_positions[i]);
        }

        // For gripper, use default parameters (no scaling)
        if (distances[8] == 0) {
            steppers[8].moveTo(target_positions[8]);  // Redundant but harmless
        } else {
            steppers[8].setMaxSpeed(MAX_SPEEDS[8]);
            steppers[8].setAcceleration(ACCELERATIONS[8]);
            steppers[8].moveTo(target_positions[8]);
        }

        if (Serial) {
            Serial.print("OK target → ");
            for (int i = 0; i < STEPPER_COUNT - 1; i++) {
                Serial.print(target_positions[i]);
                Serial.print(",");
            }
            Serial.print(gripper_state);
            Serial.println();
        }
    }
}

// ────────────────────────────────────────────────
// SETUP
// ────────────────────────────────────────────────
// Function: setup

void setup() {
    Serial.begin(SERIAL_BAUD);
    delay(200);  // give serial time to settle

    Serial.println("\n=== 9-Axis Stepper Controller (8 + Gripper) ===");
    Serial.println("Send 9 comma-separated values (8 positions + gripper state 0/1), e.g.:");
    Serial.println("  0,1200,-800,0,500,0,-300,1000,1");
    Serial.println("Negative values move opposite direction.\n");

    for (int i = 0; i < STEPPER_COUNT; i++) {
        pinMode(DIR_PINS[i],  OUTPUT);
        pinMode(STEP_PINS[i], OUTPUT);

        steppers[i].setMaxSpeed(MAX_SPEEDS[i]);
        steppers[i].setAcceleration(ACCELERATIONS[i]);
        steppers[i].setCurrentPosition(0);           // assume start at zero
    }

    // Optional: move to default/home pose on boot (uncomment if wanted)
    // memcpy(target_positions, DEFAULT_POSE, sizeof(target_positions));
    // Serial.println("Moving to default pose on startup...");
}

// ────────────────────────────────────────────────
// MAIN LOOP
// ────────────────────────────────────────────────
// Function: loop

void loop() {
    read_serial_command();

    // Run all steppers (non-blocking)
    for (int i = 0; i < STEPPER_COUNT; i++) {
        steppers[i].run();
    }

    // // Check FSR for gripper (only when closing in negative direction)
    // int fsr_value = analogRead(FSR_PIN);
    // if (steppers[8].distanceToGo() < 0 && fsr_value > FSR_THRESHOLD) {
    //     steppers[8].stop();
    //     target_positions[8] = steppers[8].currentPosition();
    // }
}

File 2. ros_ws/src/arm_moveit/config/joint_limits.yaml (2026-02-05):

# joint_limits.yaml allows the dynamics properties specified in the URDF to be overwritten or augmented as needed

# For beginners, we downscale velocity and acceleration limits.
# You can always specify higher scaling factors (<= 1.0) in your motion requests.  # Increase the values below to 1.0 to always move at maximum speed.
default_velocity_scaling_factor: 0.1
default_acceleration_scaling_factor: 0.1

# Specific joint properties can be changed with the keys [max_position, min_position, max_velocity, max_acceleration]
# Joint limits can be turned off with [has_velocity_limits, has_acceleration_limits]
joint_limits:
    grip_left_join:
        has_velocity_limits: true
        max_velocity: 5.0
        has_acceleration_limits: true
        max_acceleration: 5.0
    grip_right_joint:
        has_velocity_limits: true
        max_velocity: 5.0
        has_acceleration_limits: true
        max_acceleration: 5.0
    joint_1:
        has_velocity_limits: true
        max_velocity: 5.0
        has_acceleration_limits: true
        max_acceleration: 5.0
    joint_2:
        has_velocity_limits: true
        max_velocity: 10.0
        has_acceleration_limits: true
        max_acceleration: 5.0
    joint_3:
        has_velocity_limits: true
        max_velocity: 10.0
        has_acceleration_limits: true
        max_acceleration: 5.0
    joint_4:
        has_velocity_limits: true
        max_velocity: 10.0
        has_acceleration_limits: true
        max_acceleration: 5.0
    joint_5:
        has_velocity_limits: true
        max_velocity: 10.0
        has_acceleration_limits: true
        max_acceleration: 5.0
    joint_6:
        has_velocity_limits: true
        max_velocity: 10.0
        has_acceleration_limits: true
        max_acceleration: 5.0
    joint_7:
        has_velocity_limits: true
        max_velocity: 10.0
        has_acceleration_limits: true
        max_acceleration: 5.0
    tool_joint:
        has_velocity_limits: true
        max_velocity: 5.0
        has_acceleration_limits: true
        max_acceleration: 5.0

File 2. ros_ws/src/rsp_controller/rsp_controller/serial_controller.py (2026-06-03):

# ============================================================================
# File: serial_controller.py
# Auto-added section markers and high-level comments
# ============================================================================

# ====== Imports ======
import math
import rclpy
from rclpy.node import Node
from sensor_msgs.msg import JointState
from sensor_msgs.msg import Joy
import serial


# Hardware / motor parameters
# ====== Constants / Config ======
REDUCTION_RATIO = 4.1538
STEPS_PER_REV = 400
STAGES = [2, 3, 2, 2, 2, 2, 1, 1]


# Class: SerialController
# ====== Classes ======
class SerialController(Node):
    def __init__(self):
        super().__init__('serial_controller')

        # Subscriptions
        self.joint_state_sub = self.create_subscription(
            JointState,
            'joint_states',
            self.serial_publisher,
            10
        )

        self.joy_sub = self.create_subscription(
            Joy,
            'joy',
            self.joy_callback,
            10
        )

        # Serial port
        try:
            self.ser = serial.Serial('/dev/ttyACM0', 115200, timeout=0.1)
            self.get_logger().info("Serial port opened successfully")
        except serial.SerialException as e:
            self.get_logger().error(f"Failed to open serial port: {e}")
            raise

        # State tracking
        self.last_joint_steps = [0] * 8
        self.last_gripper_positions = [0.0, 0.0]
        self.last_sent_gripper_cmd = None      # '0' or '1'
        self.gripper_hysteresis_band = 0.015   # adjust based on your gripper jitter/noise

        # Typical gripper position ranges (ADJUST THESE TO MATCH YOUR SYSTEM)
        # Many grippers use: 0.0 = closed, positive = open
        self.gripper_open_threshold = 0.02     # above this → considered open
        self.gripper_close_threshold = 0.005   # below this → considered closed

    def joy_callback(self, msg: Joy):
        # Placeholder — implement joystick gripper control here if needed
        # Example: button 1 (index 0) to toggle gripper
        pass

    def serial_publisher(self, msg: JointState):
        if len(msg.position) != 10:
            self.get_logger().error(f"Expected 10 joint positions, got {len(msg.position)}")
            return

        # Extract gripper (first two joints) and arm joints
        gripper_pos = msg.position[:2]          # [left_finger, right_finger] or similar
        arm_pos = msg.position[2:10]            # 8 arm joints

        # Compute motor steps for the 8 arm joints
        steps = []
        for i in range(8):
            angle_rad = arm_pos[i]
            reduced_steps = angle_rad * (REDUCTION_RATIO ** STAGES[i]) * (STEPS_PER_REV / (2 * math.pi))
            step_int = int(round(reduced_steps))
            steps.append(step_int)

        # =============================================
        #          GRIPPER DECISION LOGIC
        # =============================================
        # Use average of both gripper joints (more robust against small asymmetries)
        avg_gripper = gripper_pos[1]

        # Determine desired state with hysteresis
        if self.last_sent_gripper_cmd is None:
            # First time — simple threshold
            new_cmd = '0' if avg_gripper >= self.gripper_open_threshold else '1'
        else:
            # Hysteresis: only change state if we cross a wider band
            if self.last_sent_gripper_cmd == '0':  # currently open
                if avg_gripper < (self.gripper_open_threshold - self.gripper_hysteresis_band):
                    new_cmd = '1'  # close
                else:
                    new_cmd = '0'
            else:  # currently closed
                if avg_gripper > (self.gripper_close_threshold + self.gripper_hysteresis_band):
                    new_cmd = '0'  # open
                else:
                    new_cmd = '1'

        # =============================================
        #          CHANGE DETECTION
        # =============================================
        joints_changed = steps != self.last_joint_steps
        gripper_cmd_changed = new_cmd != self.last_sent_gripper_cmd

        # For gripper position comparison we round to reduce float noise sensitivity
        rounded_current_gripper = [round(x, 5) for x in gripper_pos]
        rounded_last_gripper = [round(x, 5) for x in self.last_gripper_positions]
        gripper_pos_changed = rounded_current_gripper != rounded_last_gripper

        if not (joints_changed or gripper_cmd_changed or gripper_pos_changed):
            return  # nothing meaningful changed → skip send

        # Build command string
        joint_str = ','.join(map(str, steps))
        command = f"{joint_str},{new_cmd}\n"
        
        # Logging (very helpful for debugging random behavior)
        self.get_logger().info(
            f"Arm steps: {steps} | "
            f"Gripper pos: [{gripper_pos[0]:.4f}, {gripper_pos[1]:.4f}] "
            f"(avg: {avg_gripper:.4f}) | "
            f"cmd: {new_cmd} (was {self.last_sent_gripper_cmd}) | "
            f"sending: {command.strip()}"
        )

        # Send to Arduino / controller
        try:
            self.ser.write(command.encode('utf-8'))
            response = self.ser.readline().decode('utf-8').strip()
            if response:
                self.get_logger().debug(f"Arduino response: {response}")
        except serial.SerialException as e:
            self.get_logger().error(f"Serial write/read failed: {e}")

        # Update stored state
        self.last_joint_steps = steps[:]
        self.last_gripper_positions = gripper_pos[:]
        self.last_sent_gripper_cmd = new_cmd

    def destroy_node(self):
        if hasattr(self, 'ser') and self.ser.is_open:
            self.ser.close()
            self.get_logger().info("Serial port closed")
        super().destroy_node()


# Function: main
# ====== Functions ======
def main(args=None):
    rclpy.init(args=args)
    node = None
    try:
        node = SerialController()
        rclpy.spin(node)
    except KeyboardInterrupt:
        pass
    except Exception as e:
        if node is not None:
            node.get_logger().error(f"Unexpected error: {e}")
    finally:
        if node is not None:
            node.destroy_node()
        if rclpy.ok():
            rclpy.shutdown()


# ====== Main ======
if __name__ == '__main__':
    main()

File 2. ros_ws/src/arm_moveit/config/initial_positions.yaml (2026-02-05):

# Default initial positions for arm_description's ros2_control fake system

initial_positions:
    grip_left_joint: 0
    grip_right_joint: 0
    joint_1: 0
    joint_2: 0
    joint_3: 0
    joint_4: 0
    joint_5: 0
    joint_6: 0
    joint_7: 0
    tool_joint: 0

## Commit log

2025-10-13 first commit to new branch after adding files
    [625ZZ.stp, 68062RS.stp, 7. important-variables.xlsx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]
2026-02-05 added 3d model and test codes
    [8dof_description.csv, 8dof_description.urdf, AS5600-stepper-connector-test.SLDPRT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]
2026-02-05 removed test folder
    [625ZZ.stp, 7. important-variables.xlsx, AS5600-stepper-connector-test.SLDPRT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]
2026-02-05 renamed folder
    [68062RS.stp, AS5600-stepper-connector-test.SLDPRT, AS5600-stepper-connector-test.STL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]
2026-02-05 added ros_ws
    [arm_description.csv, arm_description.ros2_control.xacro, arm_description.urdf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]
2026-02-05 Initialize README with project details and instructions
    Added detailed project overview, repository contents, tech stack, current status, community support, and getting started instructions.
2026-05-28 added necessary documentation materials
    [ESP32-S3-PINOUT.xlsx]
2026-05-29 added header and description for frimware
    [ESP32-S3-PINOUT.xlsx]

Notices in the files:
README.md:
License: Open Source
